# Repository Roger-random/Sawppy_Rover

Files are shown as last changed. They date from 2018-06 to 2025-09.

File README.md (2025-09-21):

# Sawppy the Rover

Sawppy is a motorized model of Mars rovers Curiosity and Perseverance. It faithfully reproduces
the [Rocker-Bogie suspension kinematics](https://en.wikipedia.org/wiki/Rocker-bogie) of real
rovers and is intended to be a hardware platform for future software projects in autonomous
operation. Go forth and boldly explore the back yard, Sawppy!

All information for building Sawppy is free and public open source for anyone to build their
own. Build instructions can be found
[under the docs subdirectory](docs/).

Sawppy the Rover was inspired by [JPL's Open Source Rover project](https://github.com/nasa-jpl/open-source-rover).
Most of the differences between Sawppy and its JPL inspiration were motivated by a desire to reduce cost
and complexity. JPL's rover is designed for education, to be assembled by a school team and give a robust
foundation for structured curriculum. Sawppy is more suited for individual hobbyists like myself who are
happy to tinker and willing to make some trade-offs to lower cost.

The budget was __$500__, see [price breakdown here](docs/Price%20breakdown.md).
Getting to that price point required the following changes:

* Motorization: Instead of using gearmotors with encoders managed by RoboClaw motor controllers,
moving the wheels will be done with serial bus servo motors. For more information on these devices,
please see [this article on Hackaday.com](https://hackaday.com/2018/07/05/wrangling-rc-servos-becoming-a-hassle-try-serial-bus-servos/).
* Construction Method: Instead of using the [Actobotics construction system](https://www.servocity.com/actobotics),
Sawppy will be built from [Misumi HFS3 aluminum extrusions](https://us.misumi-ec.com/vona2/detail/110300465870/)
connected by 3D-printed plastic parts. For more information on this construction technique, please
see [this article on Hackaday.com](https://hackaday.com/2018/05/08/how-to-build-anything-out-of-aluminum-extrusion-and-3d-printed-brackets/).

These two major design goals can be summarized as: **S**ervo **A**ctuated **W**heels,
**P**rinted **I**nterconnect **F**or **E**xtrusion. The acronym SAWPIFE led to the nickedname "Sawppy".

# Development Status

**Status Update, Perseverance Landing Edition**

Generating web traffic was never an objective of my Sawppy project so I hadn't kept an eye on the
statistics, but I looked at it just now and noticed a distinct rise over the past two weeks. I
guess the successful landing of Perseverance rover on Mars motivated a lot of people to think about
3D-printing their own rover here on Earth. Welcome, fellow rover fans!

Here's a quick summary past and future for fans new and old alike:

What you see on this project page is what I now refer to as "Sawppy V1". It was my first project
that I documented with the explicit goal of helping others build their own. In contrast to most
of my other projects which were just to show an example and/or notes to remind myself later. I was
happy to see that many people have accepted my invitation and built their own rovers.
(See "Sawppy Builders" log entries on [Sawppy's Hackaday.io page](https://hackaday.io/project/158208).)
I appreciate constructive feedback submitted by Sawppy rover builders from around the world,
and have been pondering how I can evolve future Sawppy versions to address feedback.

One persistent line of feedback was that Sawppy was still too complex and expensive for some rover
fans, even though Sawppy was designed to be more affordable and simpler than the JPL Open Source
Rover that inspired it. It is true I built Sawppy for myself and others with roughly my level of
skill and budget. This translated to an audience of mostly adult hobbyists and some students of
college and high school age who can drop $500 USD on a project.

To address the audience left out of the fun by Sawppy V1, my current step in Sawppy evolution is
"Micro Sawppy". I am designing and developing a smaller, simpler, and more affordable rover. One
that I want to be accessible to elementary school age students (with adult supervision) with a
target parts cost of $100 USD. I also want to write the instructions to be more exact and prescriptive.
Sawppy V1 instructions had several areas that were left open to builder preference, something I've
learned is confusing to beginners who lacked the experience to have a preference.

Micro Sawppy also serves as my testbed for several ideas for 3D-printed rover construction that,
if successful, I want to adapt and scale up to a "Sawppy V2". This future rover would be roughly
the same size as Sawppy V1. But I want to make it easier to build, more adaptable to variations,
and a lower base cost target of $400 USD.

For latest updates and/or more details, I post my development progress to the
[Sawppy category on my personal blog](https://newscrewdriver.com/category/projects/sawppy-the-rover/).

**Sawppy version 1.0**

This milestone includes a motorized rolling chassis that is mechanically functional.
The remaining areas (electrical, software, etc.) are still very immature, just barely enough
to validate mechanical chassis function. Click this image for a YouTube video illustrating
the chassis in action, climbing a backpack that is almost double the height of wheel diameter.

Sawppy conquers a backpack (https://www.youtube.com/watch?v=SEBBMDWgtC4)

**Sawppy version 1.1**

Sawppy has received only minor mechanical changes for this milestone, including the rocker joint
angle limiter visible in action in the backpack demo video above. Most of the attention has been
on software, with contributions by the Sawppy community.

# Control Software
A Sawppy builder can now choose from many Sawppy software options. Roughly in order of power and complexity, they are:

* **Simplest**: Wired control [running on an Arduino](https://github.com/Roger-random/Sawppy_Rover/tree/master/arduino_sawppy) instead of Raspberry Pi. Created as a [backup control option](https://newscrewdriver.com/2019/05/20/sawppy-roving-with-wired-handheld-controller/) in noisy RF environments where WiFi is unreliable. It also happens to feature the bare-bones version of Sawppy geometry calculations. Wired control meant skipping all the overhead of wireless communication. Cutting out all HTML code also meant this is a good basis for other control mechanisms: send desired speed and direction into Arduino and let it handle Sawppy chassis geometry calculation.
Alternatively, it allows interfacing with anything that can communicate with an Arduino.  Here's a wiring diagram contributed by [Martin](https://hackaday.io/Plaville)
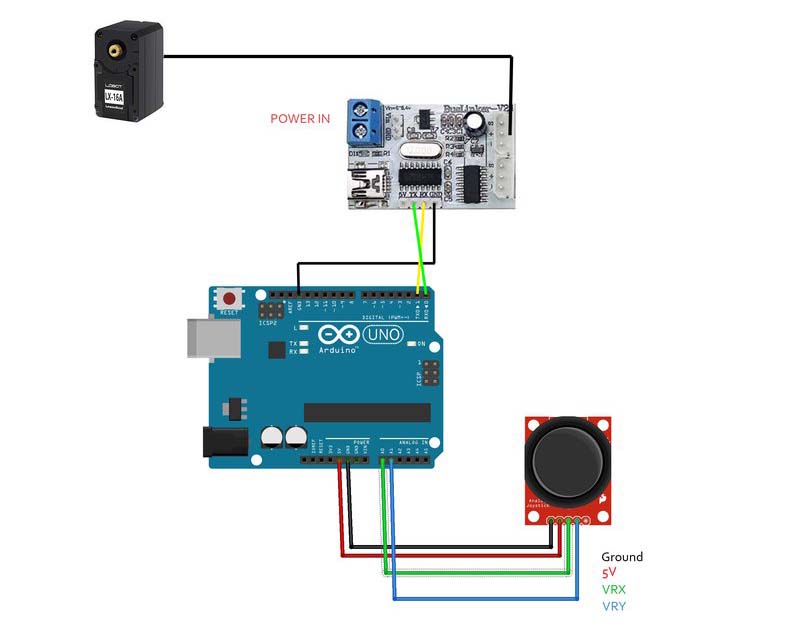
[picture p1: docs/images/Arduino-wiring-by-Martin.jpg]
Arduino wiring diagram by martin


* **Original**: HTML-based wireless teleoperation software stack [modified from SGVHAK rover](/docs/SGVHAK%20Rover%20Software.md). This was written to be easy for others to understand and modify.
* **R/C control**: [lightly modified from my SGVHAK rover software](https://github.com/mw46d/SGVHAK_Rover) by Marco Walther (mw46d) for a Raspberry Pi-based way to interface with traditional remote control receivers.

Plus several options for turning Sawppy into a [ROS](http://ros.org) robotics platform.

* **ROS Kinetic**: [heavily modified from my SGVHAK rover software](https://github.com/mw46d/Sawppy_ROS) by Marco Walther (mw46d) which translates ROS `/cmd_vel` commands into Sawppy movement. This is a good stepping stone beyond original Sawppy software.

* **ROS Melodic**: [a ground-up rewrite of a ROS-centric stack](https://github.com/srmainwaring/curio) by Rhys Mainwaring (srmainwaring) is extensive and powerful, and includes support for RViz visualation and Gazebo simulation. Going beyond responding to `/cmd_vel` commands, it also calculates `/odom` by interpolating LX-16A position encoder ~270 degree feedback into full 360 degrees. Plus visualizing rover state in RViz, and files to put a digital Sawppy in Gazebo robot simulation environment.two

* **ROS2 Humble**: [a version of Swappy the Rover for ROS2](https://github.com/mgonzs13/ros2_rover) by Miguel Ángel González Santamarta
includes a C++ and Python version of the lx16a controller and supports teleoperation with a PS3 joystick controller.  A hukuyo laser rangefinder is also supported.

# Modifications From Rover Builders

Many people who built their own Sawppy rover are also people who love to tinker
and experiment. As a result these rovers reflect the individuality of their
builder. Some of these builders have shared their work with the community,
see the [`modifications` folder](/modifications) for more information.

# Other Project Resources

* [Project page on Hackaday.io](https://hackaday.io/project/158208-sawppy-the-rover)
* [Build blog](https://newscrewdriver.com/category/projects/sawppy-the-rover/)
* [Live Onshape CAD file "Sawppy the Rover"](https://cad.onshape.com/documents/43678ef564a43281c83e1aef/w/392bbf8745395bc24367a35c/e/9bd6bbb7aba50a97523d14f2)

# Financial Support

Sawppy is shared free of charge, but builders in the United States may choose to buy some parts via
[Amazon affiliate links](docs/AmazonAssociate.md)
which will send a small sales commission to Sawppy's creator.

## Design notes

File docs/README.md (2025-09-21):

# Instructions

This directory has information for building your own Sawppy the Rover.
Some of the tools required are listed in the [tools list](Tools.md).

All Sawppy information is shared freely. Those who wish to support this
project may choose to purchase certain parts via
[Amazon affiliate links.](AmazonAssociate.md)
(This does not increase your purchase price.)

## 3D Printed Components
[General overview](Print%20Overview.md) of 3D-printed rover parts.

Details:
* [Servo accessories](Print%20Servo%20Parts.md)
* [Steering knuckle](Print%20Steering%20Knuckle.md)
* [Fixed knuckle](Print%20Fixed%20Knuckle.md)
* [Wheel](Print%20Wheel.md)
* [Wheel hub](Print%20Wheel%20Hub.md)
* [Corner Steering Joints](Print%20Corner%20Steering%20Joints.md)
* [Suspension Bogie Joints](Print%20Suspension%20Bogie%20Joints.md)
* [Suspension Rocker Joints](Print%20Suspension%20Rocker%20Joints.md)
* [Main Body Box Corners](Print%20Body%20Box%20Corners.md)
* [Differential](Print%20Differential.md)
* [M3 Nut Installation Tool](Print%20M3%20Installation%20Tool.md)

## Customized Metal Components
* [15mm square aluminum extrusion beams](Misumi%20HFS%203.md)
* [8mm diameter shafts](Shaft8mm.md)

## Mass-produced Components
* __Turnbuckles__ are used to connect both sides of rocker-bogie suspension together,
see the end of [this document](AssembleRocker.md). The two connection endpoints
need to accomodate M3 fasteners as used in the rover, and the distance between
connection endpoints should be roughly 5cm - 7.5cm. Example:
[Hobbypark 16617](https://www.amazon.com/dp/B01H5PZKMK)
is seen in the assembly pictures.
* __"608" Bearings__ are widespread. It's the type used in products like
rollerblades, skateboards, and scooters. Since Sawppy does not run bearings at
high speeds or put heavy loads on them, expensive
[industrial strength 608 bearings](https://www.mcmaster.com/608-ball-bearings)
are unnecessary. Shop around for
[inexpensive alternatives](https://www.amazon.com/dp/B073ST742Z),
they'll probably suffice for a hobbyist rover.
* __M3 Heat Set Inserts__ give metal threads for 3D-printed parts which are more
durable than threads tapped into printed plastic. Sawppy's default design is sized
for [these inserts](https://www.amazon.com/gp/product/B077CHFGVT) on my printer,
and reportedly works well with [these inserts](https://www.mcmaster.com/94180a333)
as well.
* [Purchased Parts List](Parts%20List.md)

## Mechanical Assembly
For an overview of the construction technique used here, combining aluminum extrusion beams with
3D printed connectors plus using design-specific M3 nut installation tools, please
[see this article on Hackaday.com](https://hackaday.com/2018/05/08/how-to-build-anything-out-of-aluminum-extrusion-and-3d-printed-brackets/).

If any part of the assembly instructions are unclear, consult
[the CAD file](https://cad.onshape.com/documents/43678ef564a43281c83e1aef/w/392bbf8745395bc24367a35c/e/9bd6bbb7aba50a97523d14f2)
to see how parts are supposed to fit together.

* [Servo Actuator Module](AssembleActuatorModule.md)
* [Wheel Drive Modules](AssembleDriveModules.md)
* [Suspension Pivot Joints](AssemblePivotJoints.md)
* [Main Rover Body](AssembleBody.md)
* [Suspension Differential](AssembleDifferential.md)
* [Suspension Bogie](AssembleBogie.md)
* [Suspension Rocker and final assembly](AssembleRocker.md)

Once all the wheels are attached to the suspension via M3x16mm bolts, your Sawppy will be mechanically complete!

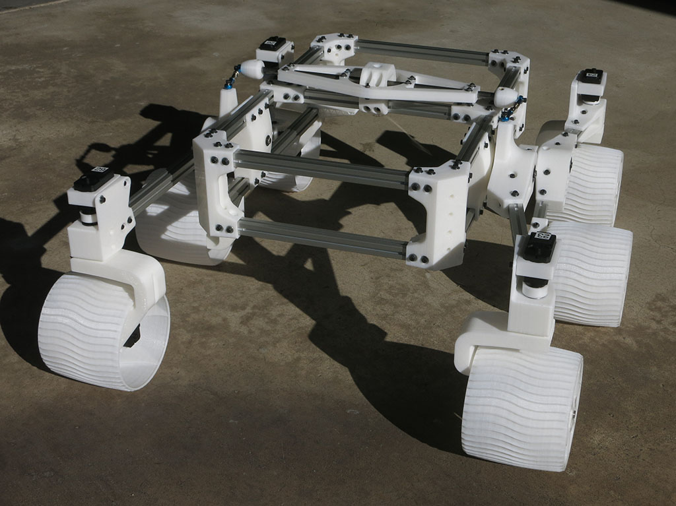
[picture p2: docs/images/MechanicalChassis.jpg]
Mechanical chassis


## Electronic Schematic

A bare-bones Sawppy build will have the following electronic components:
* A 2-cell lithium polymer battery. (Visible in pictures is a 30C 5200mAh RC
monster truck battery)
* A power switch
* Because the battery can deliver up to 150A and nothing on the rover can
tolerate more than a few amps, a [10A fuse to protect against short circuits](https://newscrewdriver.com/2018/06/06/powering-sawppy-the-rover/  ).
* A volt meter to monitor battery voltage.
* A [voltage regulator](https://newscrewdriver.com/2017/07/27/powering-the-raspberry-pi-3-with-mp1584-voltage-step-down-converter/) to convert battery power to 5V.
* A Raspberry Pi 3 powered by 5V regulator output, either via micro USB port or GPIO voltage pins.
* A USB cable connecting Raspberry Pi 3 to serial bus translator board.
* Ten serial bus servos connected in parallel to the translator board. See
[documentation on wiring details](wiring/Wiring.md) contributed by
[knickels](https://github.com/NickelsLab).

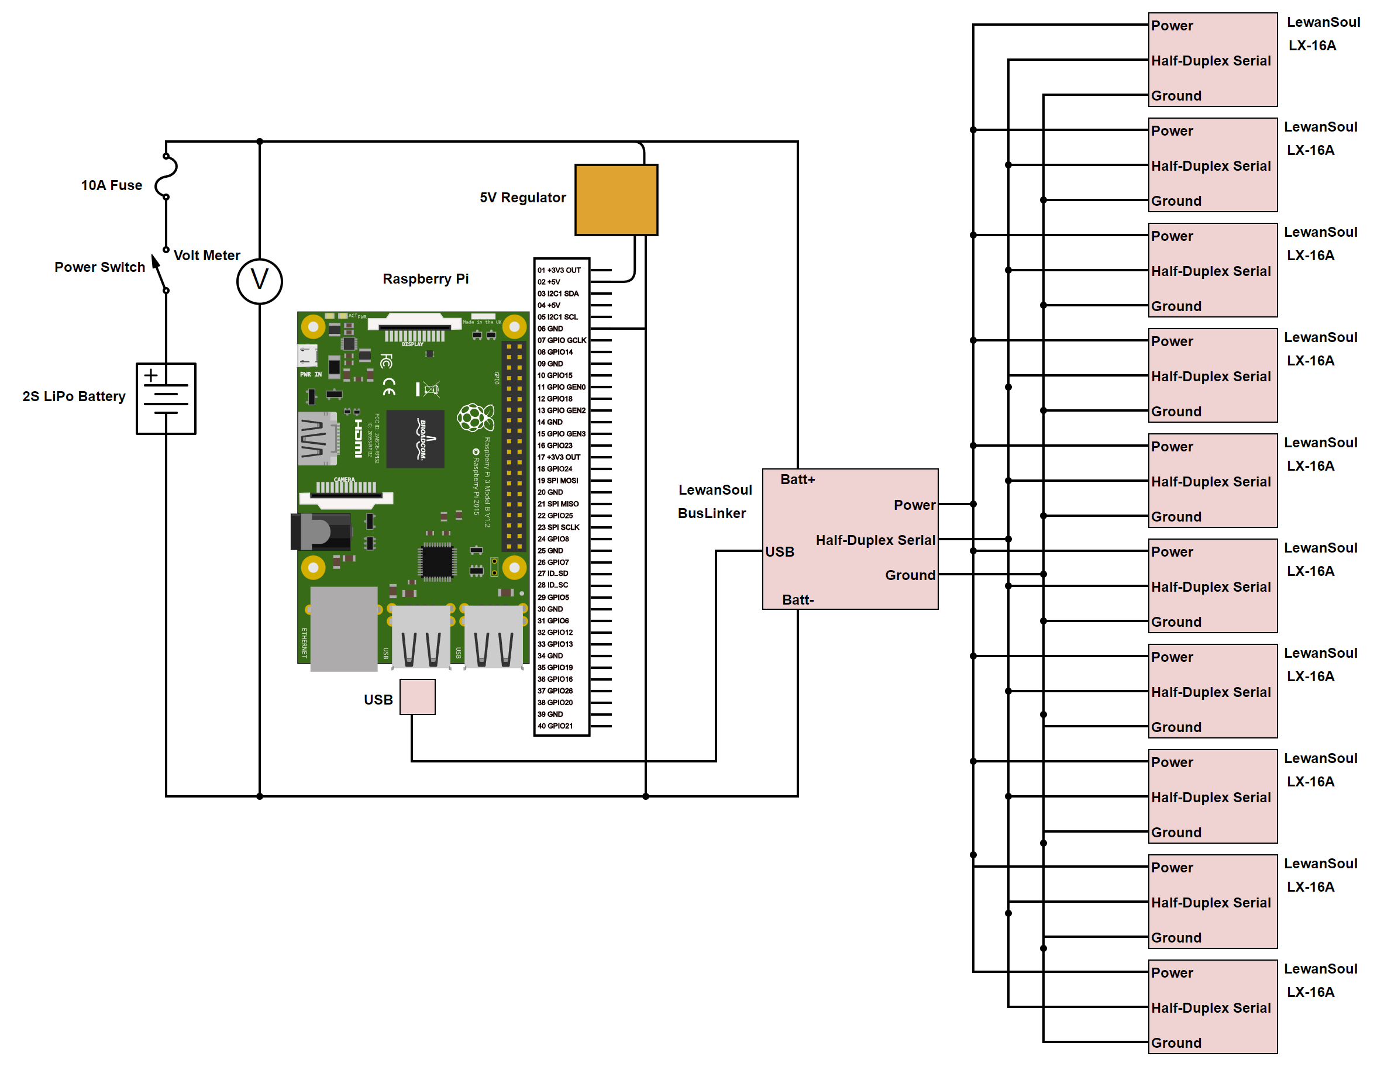
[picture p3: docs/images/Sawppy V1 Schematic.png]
Schematic

[Click here to open schematic in Digi-Key's web-based Scheme-It tool.](https://www.digikey.com/schemeit/project/sawppy-v1-EKLPGFO401M0)

Optional components visible in some Sawppy pictures:
* A [USB webcam](https://newscrewdriver.com/2018/06/19/sawppy-the-backyard-rover/).
* Google [AIY Vision kit](https://newscrewdriver.com/2018/06/18/sawppy-the-rovers-mast-cameras/).
* A dual-band wireless router for [greater range and access to 5GHz band](https://newscrewdriver.com/2018/07/15/sawppy-the-rover-receives-wifi-upgrade-increases-range/).

# Control Software
A Sawppy builder can now choose from many Sawppy software options. They are documented in [README.md#control-software](../README.md#control-software)

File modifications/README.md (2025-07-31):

# Modifications

This directory tracks modifications to Sawppy made by other rover builders.

## Bob Krause, Inventor Studios

A FIRST Robotics team improved Sawppy's design with better configurability.
See more information [here](bob_krause/README.md)

## Quinn Morley

The Qualification Model Rover Demonstrator for Deep Drilling is a scaled-up
version of Sawppy which will serve as a prototype drilling platform testbed.
See more information on [design blog](https://www.quinnmorley.com/2019/02/qmrd3-rover-testbed.html)
and [Github repo](https://github.com/Shootquinn/QMRD3)

## Marco Walther (mw46d)

* Dynamixel AX-12 brackets
* 25D geared motors with encoders

More info [here](Marco_Walther/README.md)

## Kevin Nickels, Trinity University
Trinity Robotics version of Sawppy is named TRIPPY, and has the following revisions:
 * LewanSoul LX-224 brackets
 * LewanSoul LX-224 brackets with captured nuts instead of threads
 * Used M3 Screws as steering axle SetScrews instead of heat-set inserts
 * Modified Arduinio Nano Joystick to use RJ9 connector & phone cord
 * Added holster to hold joystick when not in use

 See more information [here](kevin_nickels/README.md)

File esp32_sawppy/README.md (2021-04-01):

# ESP32 Sawppy Brain
This directory is a PlatformIO project for a Sawppy brain built using an ESP32 development kit.
Using the ESP-IDF framework, individual components are organized into FreeRTOS tasks.

This is written to support Micro Sawppy development, which uses generic RC micro servos and
DRV8833 DC motor driver ICs. It is not yet able to support LX-16A serial bus servos used in
Sawppy V1.

For more details please see project build log: https://newscrewdriver.com/tag/micro-sawppy/

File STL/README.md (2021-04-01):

# Sawppy Rover STL
This directory contains a snapshot of Sawppy rover STL files.
These files will be some distance behind the state of the art, but guaranteed to have been tested.
Onshape CAD file that generated these STL files is available publicly. See documentation directory
for details.

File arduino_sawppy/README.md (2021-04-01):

# Arduino Sawppy Controller
This directory is an Arduino sketch, intending to give Sawppy rover a wired joystick controller
alternative to default WiFi wireless control. Target platform is ATmega328-based Arduino Nano.

Target rover platform is Sawppy V1, based around the LewanSoul/HiWonder LX-16A serial bus servo.
It has not (yet?) been adapted to rovers built on different hardware.

More details on Sawppy build blog, start here and look at adjacent blog entries.
https://newscrewdriver.com/2019/05/20/sawppy-roving-with-wired-handheld-controller/

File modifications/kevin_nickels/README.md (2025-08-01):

# Modifications made by Kevin Nickels, Trinity University

Dr. Nickels has made a TRIPPY - a variant of the Sawppy rover at Trinity University in San Antonio, TX.  He has made several minor modifications to the design during the build.   The name TRIPPY evolved from Trinity-SAWPPY, but could stand for "Trinity Robotics Instructional Planetary Platform".  It's purpose is to give Engineering students at Trinity University in San Antonio a robust platform to develop on top of, and to learn about the world of open-source hardware.

## Table of Contents
 * [LewanSoul LX-224 brackets](#lx-224-servos)
 * [Used M3 Screws as steering axle SetScrews instead of heat-set inserts](#m3-setscrews)
 * [Modified Arduinio Nano Joystick to use RJ9 connector & phone cord](#joystick-controller-modifications)
 * [Added holster to hold joystick when not in use](#joystick-holster)

## Overview

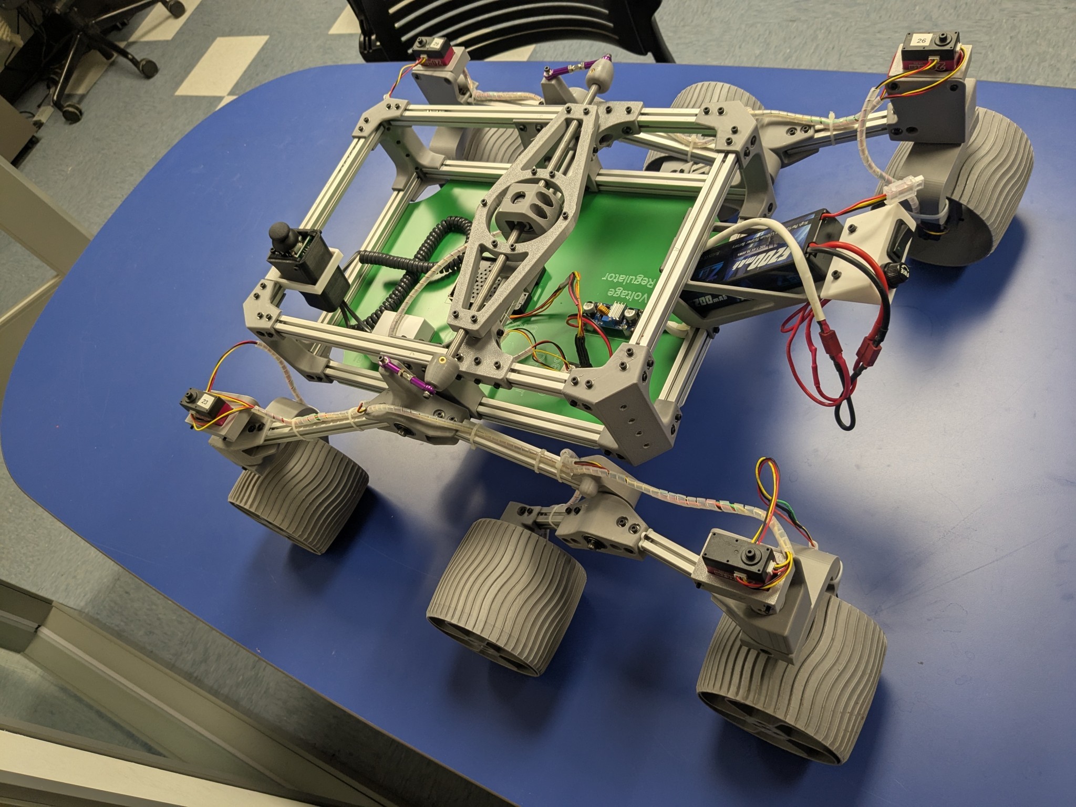
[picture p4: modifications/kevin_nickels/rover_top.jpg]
rover_top

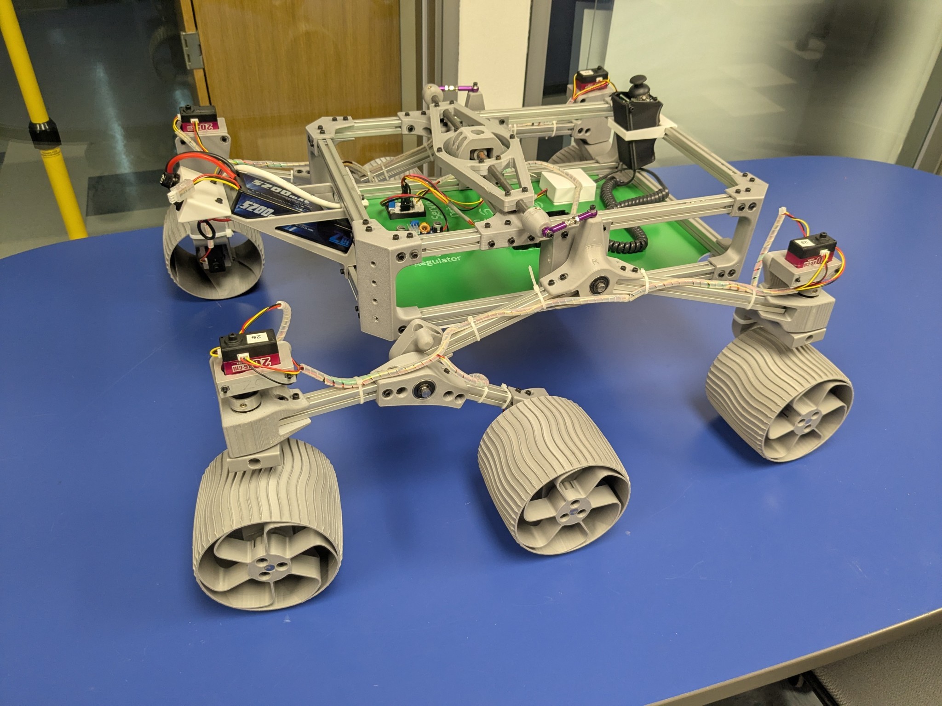
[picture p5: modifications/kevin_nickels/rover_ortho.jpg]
rover_ortho


## LX-224 Servos

The [LX-16A](https://www.amazon.com/Hiwonder-LX-16A-Robotic-Controller-Control/dp/B073XY5NT1) was out of stock when I went to acquire my parts, so I ordered the very similar [LX-224](https://www.amazon.com/LX-224-Serial-Controller-Connectors-Bearing/dp/B0817YWHNL).  I created a LX-224 bracket per the original design, see [my OnShape Sawppy Copy](https://cad.onshape.com/documents/7f40e51e085505c60163b9a8/w/9308f0417bc9c0c20e3ccf9f/e/5f2c482cad123d78f392508a), LX-224 branch, LX-224 Part Studio.
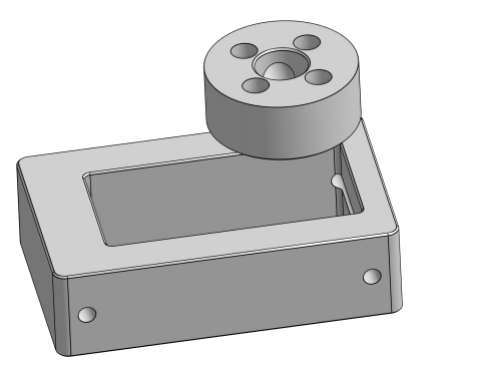
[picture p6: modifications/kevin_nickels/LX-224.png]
LewanSoul LX-224 bracket
 

Since I've had problems with threads, and even threaded inserts, pulling out of plastic before, I also generated an alternative bracket in [the same OnShape CAD, branch LX-224 Bracket w Captured Nuts](https://cad.onshape.com/documents/7f40e51e085505c60163b9a8/w/f72775573146bf34f38f572e/e/5f2c482cad123d78f392508a).  This is designed to be used with [M3x40mm screws](https://www.amazon.com/BNUOK-120pcs-Socket-Threads-Spanner/dp/B0DJQFXKHG/).

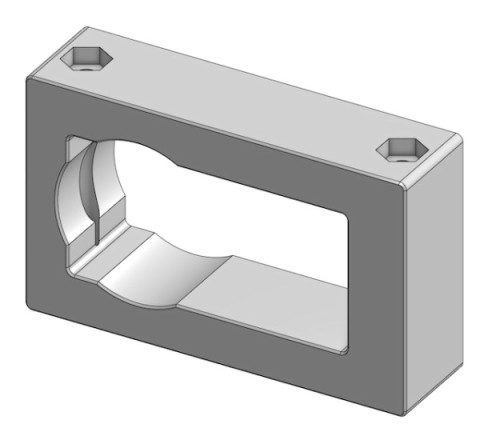
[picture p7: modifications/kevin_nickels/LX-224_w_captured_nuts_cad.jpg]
CAD rendering of LX-224 servo bracket featuring captured nuts for enhanced strength, showing the bracket attached to a steering knuckle within a mechanical assembly.


## M3 SetScrews
As was mentioned in the Discussion section of [CJ - a sawppy variant](https://hackaday.io/project/165094-cj-a-sawppy-variant) on Hackaday, some of us have had issues with heat-set inserts pulling out.  As shown in this CAD and the pictures below, I ended up printing a Nut Carriage to get good strength and print resolution in the XY direction, then printing the knuckle in the standard orientation, so that the M3 nut won't spin when tightened against the flat in the 8mm shaft.  Then, I used an M3x16 screw as a setscrew instead of the tiny ones called out in the original.  We'll see how this holds up over time!

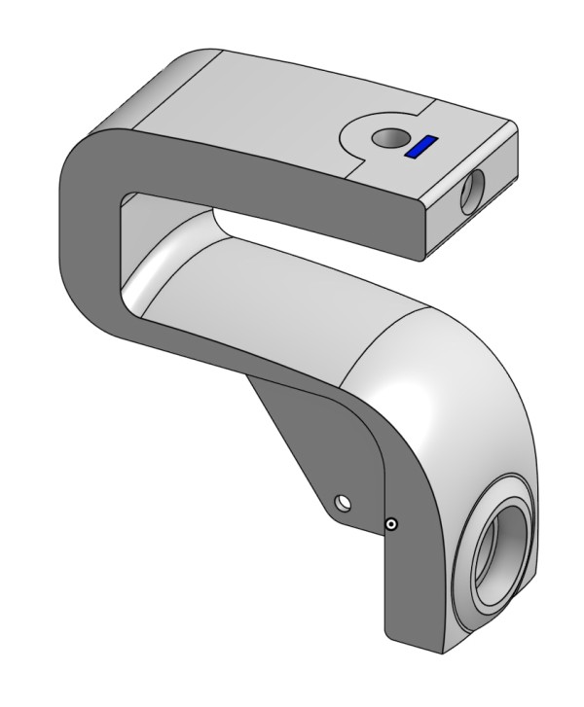
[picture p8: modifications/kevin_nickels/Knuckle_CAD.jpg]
CAD of steering knuckle with nut insert

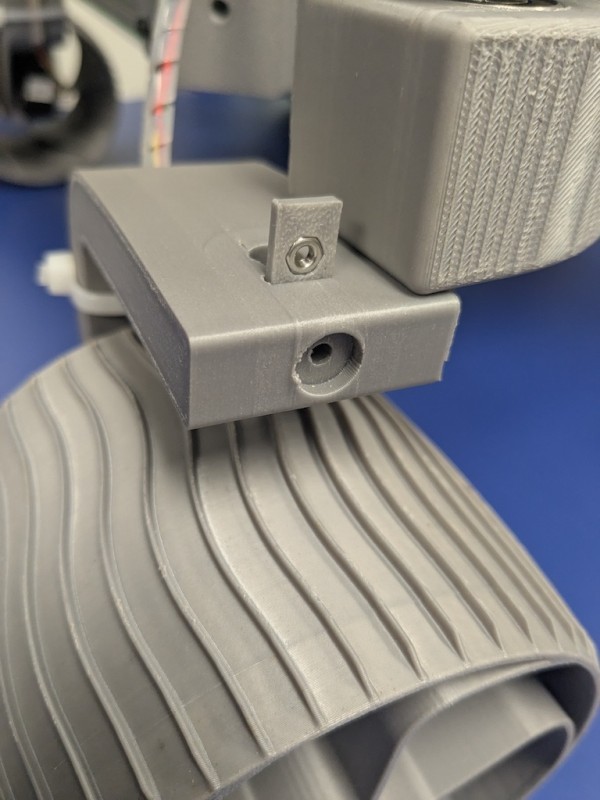
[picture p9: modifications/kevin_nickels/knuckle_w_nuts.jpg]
image of steering knuckle with nut insert

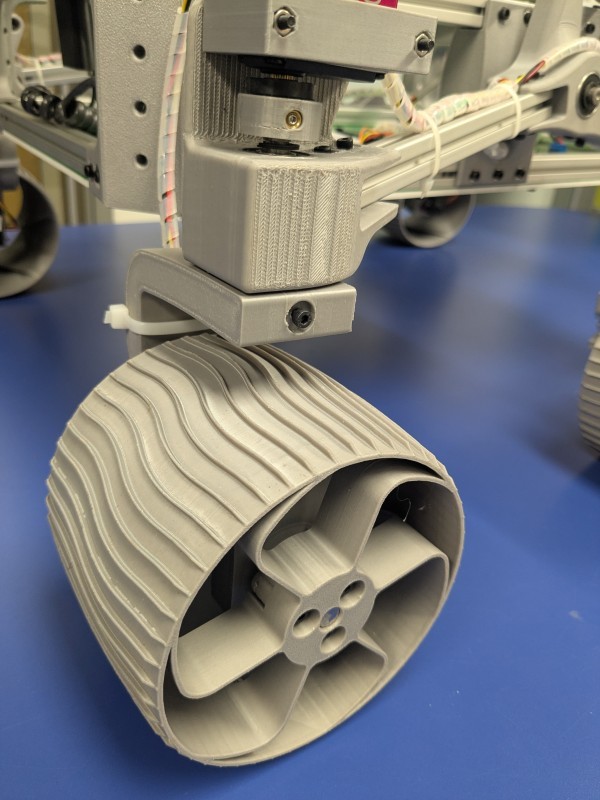
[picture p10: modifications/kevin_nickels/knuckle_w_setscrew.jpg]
image of steering knuckle with nut insert installed


## Joystick Controller Modifications
I also modified the [Handheld Arduino Joystick controller](https://cad.onshape.com/documents/47ee84411a76e86eae57ea0f/w/f70ae835a2d548c4b95fa46e/e/c8538a52492e953cdcdd3db5) to accept an [RJ9](https://www.ebay.com/itm/317094616170) so that I can connect my controller to my rover with a standard coiled phone cord.

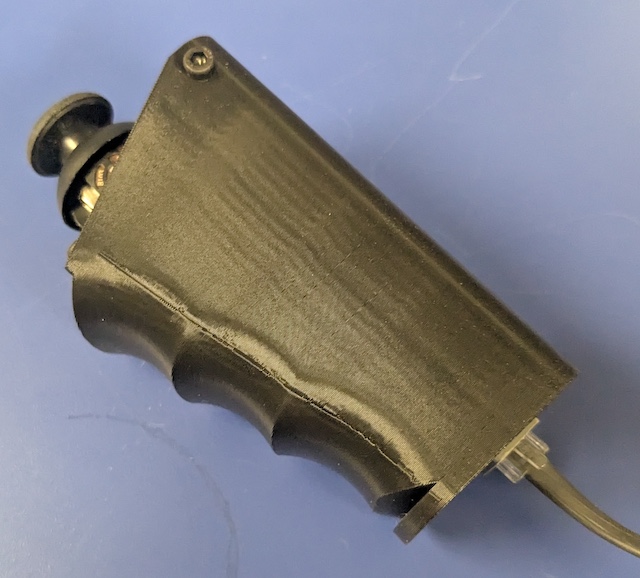
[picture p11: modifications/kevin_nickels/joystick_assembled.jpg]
Picture of assmbled joystick

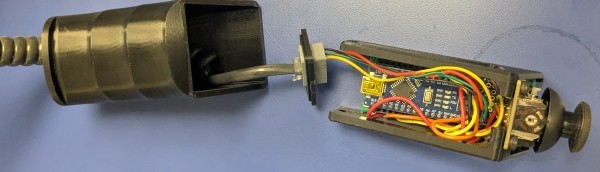
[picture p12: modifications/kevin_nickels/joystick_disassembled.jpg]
Picture of disassembled joystick

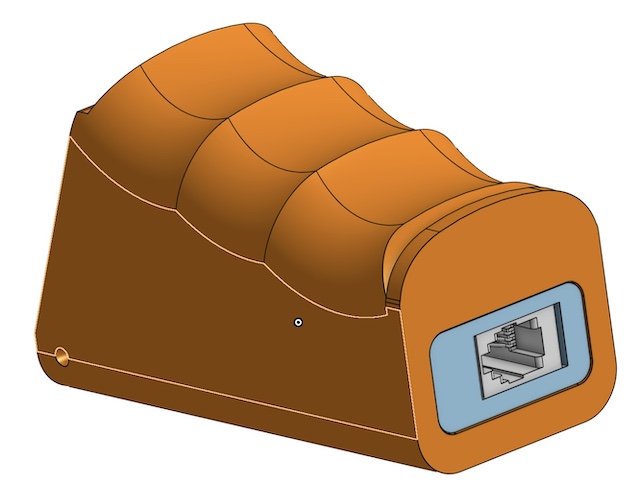
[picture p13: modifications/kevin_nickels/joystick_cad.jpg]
CAD of joystick with RJ9


## Joystick Holster
Finally, I added a holster to the [Handheld Arduino Joystick controller](https://cad.onshape.com/documents/47ee84411a76e86eae57ea0f/w/f70ae835a2d548c4b95fa46e/e/d239459ff7d458760645b579) to accept an [RJ9](https://www.ebay.com/itm/317094616170) so that I can connect my controller to my rover with a standard coiled phone cord.

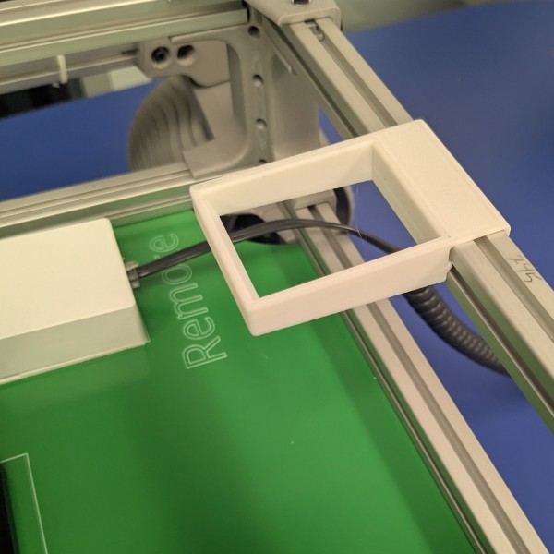
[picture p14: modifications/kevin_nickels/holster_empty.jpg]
Image of holster without joystick

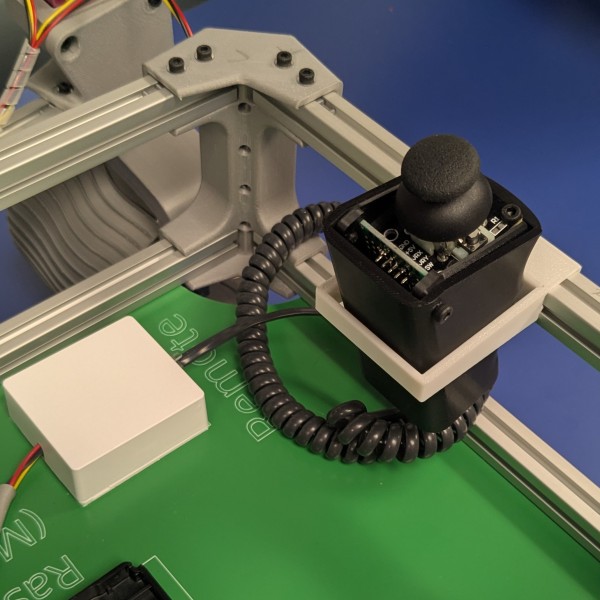
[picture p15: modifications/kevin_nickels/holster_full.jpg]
Image of holster with joystick


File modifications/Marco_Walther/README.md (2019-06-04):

# mw46d Additions

* I created some extra parts to interface the Dynamixel AX-12's with the original parts. But my LX-17 servos arrived in time, so I did not really try the AX-12s.
* I created motified knuckles to use 25D geared motors with shaft-encoders.
(https://www.aliexpress.com/item/6V-100-210-300RPM-Encoder-Motor-DC-Gear-Motor-with-Worm-Gear-Torque-Locking/32914332902.html) I'm using the 100rpm versions of the motor
and they work very well and allow me to get the encoder readings and use those for speed/distance calculations. The only downside is, that I have to deal with many more
cables:-( Originally, each side had just three, now I have 3 (for the steering servos) + 3 * 6 (for the drive motors).
* A nice little Display just for fun;-) Found it on the original NASA JPL rover model and liked it;-)

A little night excursion: https://youtu.be/rvCmtjlanaQ

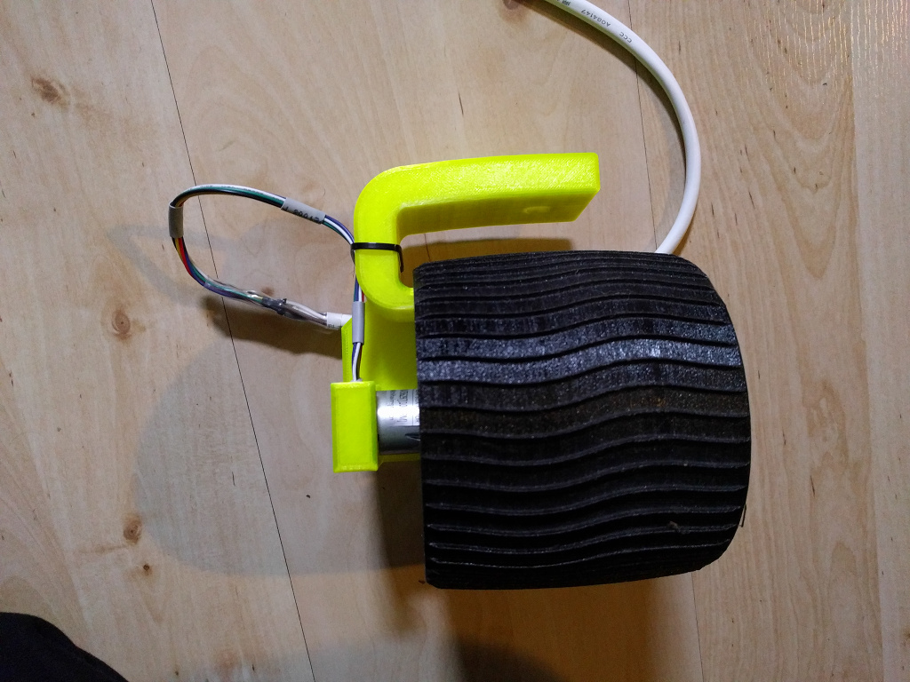
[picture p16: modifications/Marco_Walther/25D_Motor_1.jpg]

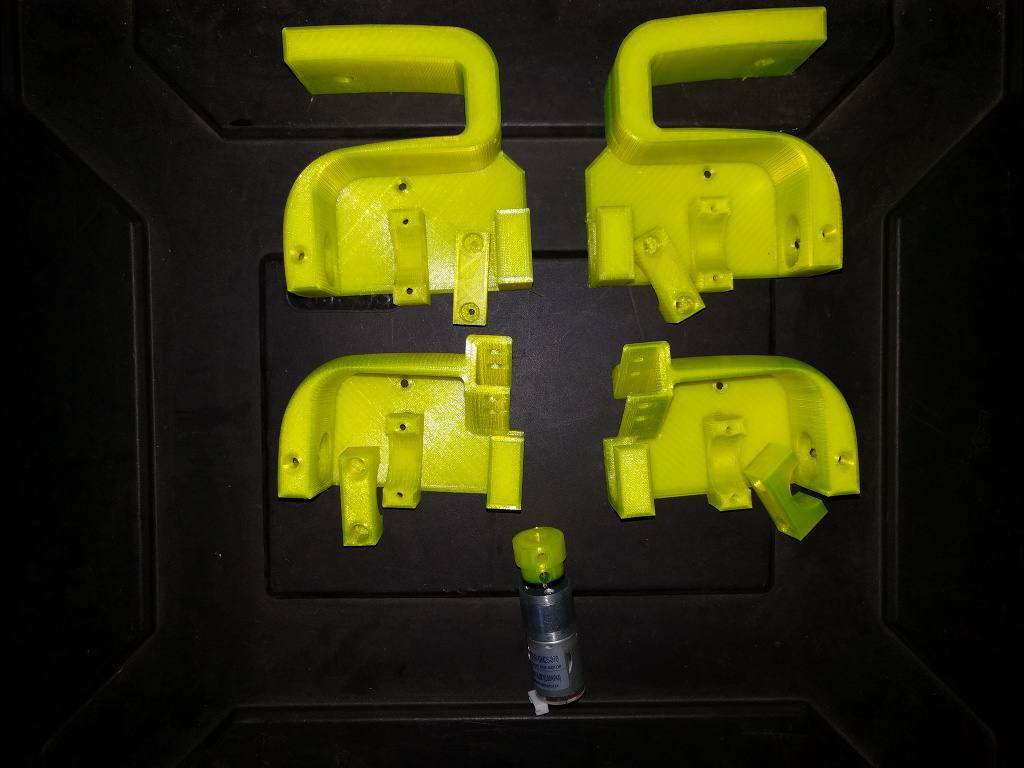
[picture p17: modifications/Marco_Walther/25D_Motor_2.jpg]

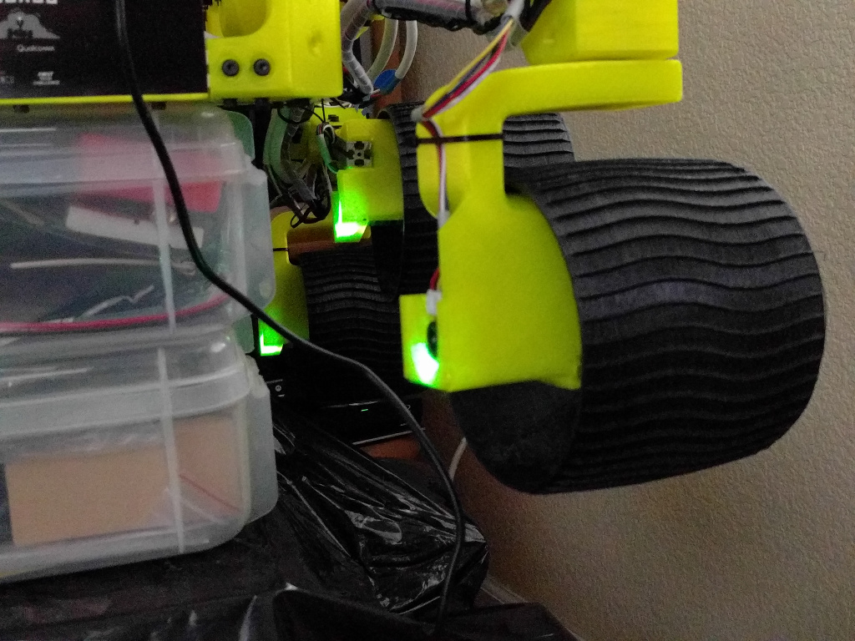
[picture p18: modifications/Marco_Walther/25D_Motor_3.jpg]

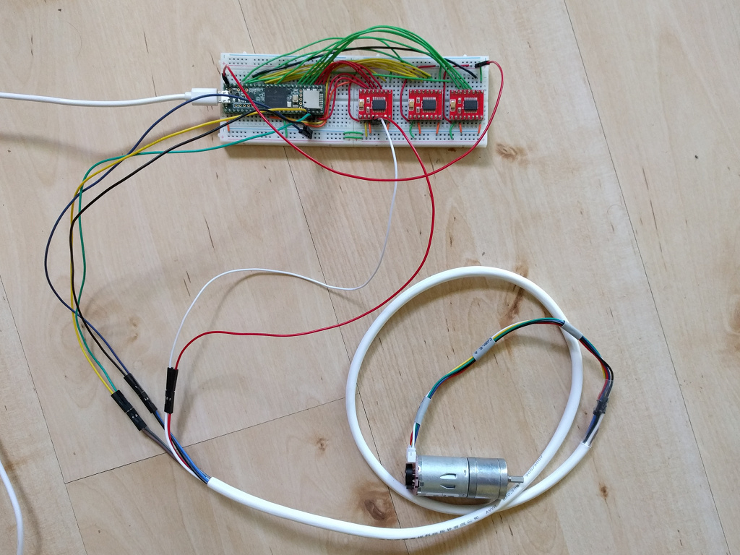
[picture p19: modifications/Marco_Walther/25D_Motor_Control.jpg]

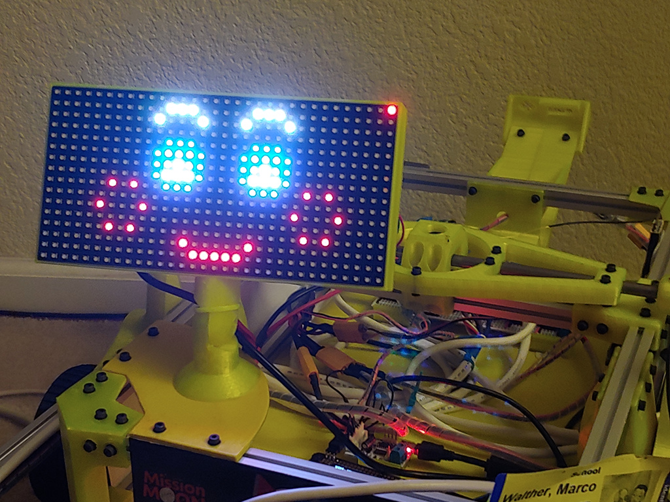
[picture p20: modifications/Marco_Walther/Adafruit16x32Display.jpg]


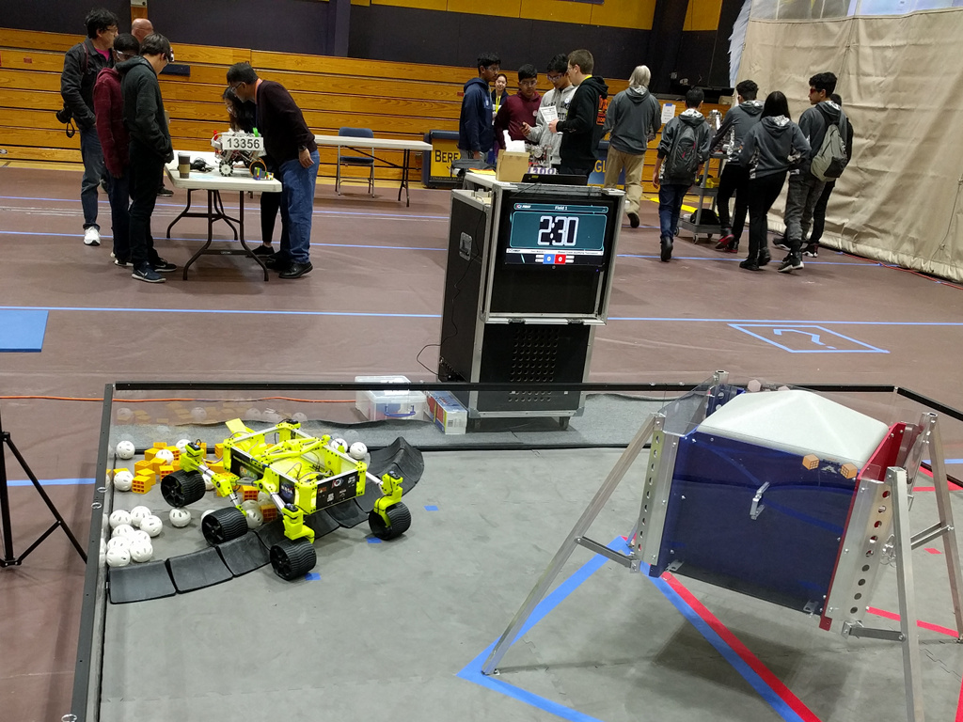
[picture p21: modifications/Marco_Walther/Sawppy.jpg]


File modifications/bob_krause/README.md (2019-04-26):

# Bob Krause, Inventor Studios

(The following information was first posted on Sawppy's Hackaday.io project
discussions section [here](https://hackaday.io/project/158208-sawppy-the-rover/discussion-116870))

_____

Our focus at this point is to increase the configurability of the design, as
you can see in the list of changes we’ve made so far that’s included below. 

* Wheel width can be changed
  * Wheel width changeable
  * Steerable knuckle width varies with wheel width
  * Fixed knuckle width varies with wheel width
* Wheel rim and tire can be printed as separate parts of a dual-extrusion
printer job
* Beam width & height can be changed
  * All 3D printed components that accept beams varies based on beam dimensions
* LX-16A brackets now accept heat-sets so that servos are held more tightly

* The geometry of the LX-16A bracket changed. 
  * The orientation of the servo is rotated 180 degrees to fit narrow knuckles
  and narrow tires.

The area we’re focusing on next is support for drive-train and control systems
that will move the bot much (much) faster than the LX-16A servos currently
allow. The first step in that direction is to design in FTC-compatible (First
Technical Challenge) components, which we have an almost endless supply of
parts laying around the lab. Driving a bogie suspended robot around on rough
terrian at high speeds will likely require adding shock dampeners to the
suspension.

Our longer-term aspiration is to create a more flexible robot design tool
that allows designers to create robots with different dimensions,
drive-trains, suspensions, control systems, and accessories.

We’ve made our copy of the OnShape document public. It’s named
SawppyRover.neobobkrause. You can link to it here
https://cad.onshape.com/documents/aaa3eec885d174f48744d770/w/a9ccb2ae8a9fa3bfab65a3f5/e/02e39956ce53a7a4a720a4aa

Here are some shots of some wheels and knuckles we've printed that are
narrower (65mm). One wheel has a TPU tire on a PLA rim. The other rim was
printed using transparent PETG. The third photo shows the narrow fixed knuckle
from the inside. Also note that the orientation of the servo has been rotated
180 degrees.

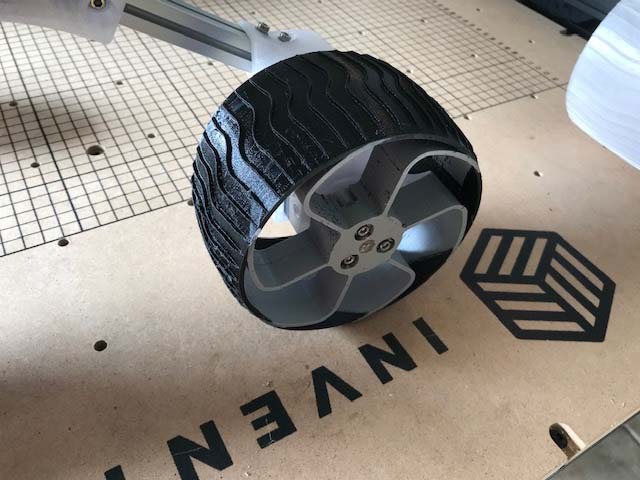
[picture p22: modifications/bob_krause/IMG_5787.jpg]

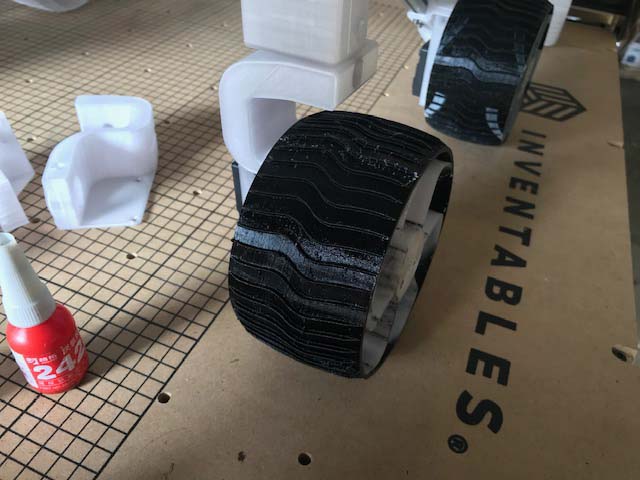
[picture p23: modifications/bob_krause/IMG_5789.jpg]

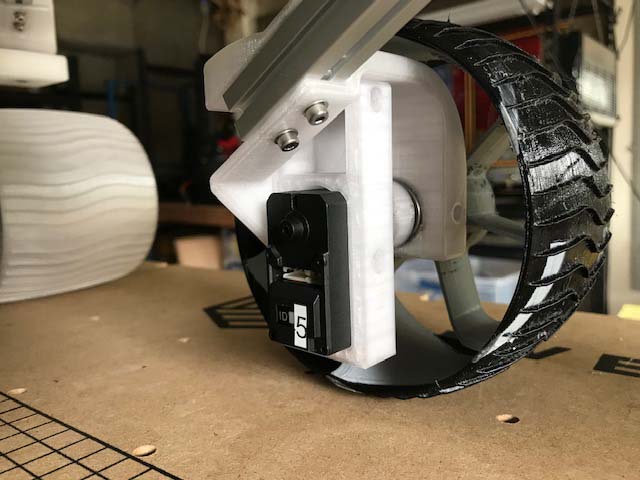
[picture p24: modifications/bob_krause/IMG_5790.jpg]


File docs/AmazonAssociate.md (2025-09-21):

# Support Sawppy via Amazon Associates Program
Sawppy the Rover is a project done out of love of our interplanetary robotic
explorers Curiosity and Perseverance. Sawppy's design and instructions for
construction are shared with other rover lovers free of charge under the
permissive MIT license.

Some very generous people have offered to donate to
help the project. I have declined offers of direct donation, but I have
set up an Amazon Affiliates account based on suggestion. If an aspiring
rover builder buys components from Amazon (USA) using the links
below, they will pay the same price but Amazon will send a (very small)
percentage of the sale to me as sales commission.
Here is the boilerplate disclosure:
_As an Amazon Associate I earn from qualifying purchases._

I have other links to Amazon products scattered throughout Sawppy
documentation, but they are generic links that do not earn commission.
This is the only page with affiliate links.

__Name__ | __Specific__ | __Generic__ | __Comments__
--- | --- | --- | ---
_**Mechanical**_ |
LX-16A Bundle | [Hiwonder](https://amzn.to/2WAm4Wl) | | Each bundle includes 5 servos and 1 BusLinker. A rover needs 10 servos and 1 BusLinker.
LX-16A | [Hiwonder](https://amzn.to/2z0VVqV) | | Individual replacements, or if bundle is not available.
BusLinker | [TTL Board](https://amzn.to/2T4V8vZ) | | Only one needed per rover. Do not need to buy separately if buying LX-16A bundle.
Turnbuckle | [Hobbypark](https://amzn.to/3cCZ5Qg) | | Eyes at end should fit M3 fasteners
Bearings | [SACKORANGE](https://amzn.to/3fMBiiG) | [608](https://amzn.to/2WyPHHO) | Inexpensive generics are fine
M3 Heat Set Inserts | [Initeq](https://amzn.to/2WWCF5Q) | | 3D printed parts are sized to this outer diameter
Cable sleeve | [Techflex](https://amzn.to/366gdLy) | | Wire management
_**Electronics and Communication**_ |
Servo Cable Connectors (LX-224) | | [JST2.0 P3 Connectors](https://www.amazon.com/80Pcs-JST-2-0-Connector-Plug/dp/B0DMW522GM) | To connect LX-224 servos to BusLinker
Servo Cable Connectors (LX-16A) | | [Mini-SPOX Pins](https://www.newark.com/molex/08-70-1040/contact-socket-22awg-crimp/dp/54H5573) [Mini-SPOX  Housing](https://www.newark.com/molex/50-37-5033/connector-rcpt-3pos-1row-2-5mm/dp/57H1785)| To connect LX-16A servos to BusLinker
Crimper for Mini-SPOX | | [iCrimp XH2.54mm](https://www.amazon.com/dp/B00YGLKBSK?th=1) | To crimp Mini-SPOX pins
Raspberry Pi | [Pi 3 Model B](https://amzn.to/3cArxSI) | [Raspberry Pi](https://amzn.to/2AythOm) | 3B+ now available, Pi 4 should also work
microSD Card | [Sandisk Extreme 32GB](https://amzn.to/3bET8AS) | | For Raspberry Pi
Wireless Router | [Asus RT-AC1200](https://amzn.to/2TcYBst) | | (Optional) Easier to find a channel on 5GHz WiFi in crowded places.
Arduino Nano | [ELEGOO](https://amzn.to/3bvAFXy) | [Other Clones](https://amzn.to/2LzvqLK) | (Optional) backup [wired control](https://github.com/Roger-random/Sawppy_Rover/tree/master/docs#wired-arduino)
Joystick module | | [WMYCONGCONG](https://amzn.to/3fNR0KB) | (Optional) backup [wired control](https://github.com/Roger-random/Sawppy_Rover/tree/master/docs#wired-arduino)
_**Power System**_ |
Battery | [Floureon](https://amzn.to/3dQJ21r) | [2S LiPo](https://amzn.to/2WWz2ge) | Typically sold for remote control cars/boats/aircraft.
Battery Connector | [Adoreco](https://amzn.to/2WZhikp) | [Deans T Plug](https://amzn.to/3dPsbfh) | Commodity plug
Inline Fuse Holder | [Nilight](https://amzn.to/3cCqfXf) | | Holds automotive style blade fuses
Fuse Assortment | [BESTTOYHOME](https://amzn.to/2WY3zKA) | | 5A fuse allows normal operations while protecting against abuse
5V Regulator | [Qunqi](https://amzn.to/2AyxH7T) | [MP1584EN](https://amzn.to/361HHlK) | Converts raw battery power to 5V for Raspberry Pi
Battery Charger | [Tenergy TB6-B](https://amzn.to/3dNjMZV) | [LiPo Charger](https://amzn.to/2TcliwL) | Cell balancing capability preferred
Power Switch | [Conwork SPST](https://amzn.to/2ApRB4L) | | (Optional) This one fits in my power panel
Voltage LED | [Baite](https://amzn.to/364aeqD) | | (Optional) This one fits in my power panel
Low Battery Alarm | [Woafly](https://amzn.to/3fVtOdt) | | (Optional) Connected to battery's balancing plug

### Legend:
* __Name__ used in Sawppy documentation.
* __Specific__ This is the specific item for my own Sawppy and I am happy with my first hand experience.
* __Generic__ This is the general category of items. Not specifically on board my rover but they should all work just fine. (If it's a link to a specific item: I was not happy with my experience, but it was nominally usable.)
* __Comments__ Addendum

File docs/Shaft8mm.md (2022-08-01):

# 8mm metal shafts

Sawppy the Rover uses 8mm shafts anywhere there is a rotary motion that whose load is borne by 608 type bearings.
* Wheel axle drive shaft for all 6 wheels.
* Steering shaft for 4 corner motors.
* 2 Suspension bogie pivot point, one on each side.
* 2 Suspension rocker pivot point, one on each side.

Below are instructions on how to build your own shafts.

---

Sawppy also uses an 8mm shaft as main backbone for the differential that spans width of the rover. This shaft is
300mm long and hosts no retaining clips, so there are no grooves to cut. It host set screws at either end,
but they do not convey torque and detents are not required to be cut.

## Shaft stock selection

Any metal shaft should work, as long as it has the appropriate 8mm diameter to fit snugly within 608 type bearings used.
As these shafts are not spun to high speeds, carry high torque, or mesh with other machinery, Sawppy does not require
high precision industrial machinery shafts. (Example: unnecessarily expensive high precision shafts from
[Misumi](https://us.misumi-ec.com/vona2/detail/110300086920/?ProductCode=SFMR8-300)
and [McMaster-Carr](https://www.mcmaster.com/1265k64)) Low precision round bar stock are a fraction of the cost and will
suffice. The worst that would happen with low precision shafts is that wheels may be a little wobblier.

Aluminum shafts (example: McMaster-Carr [catalog #4634t34](https://www.mcmaster.com/4634t34)) are inexpensive and strong
enough for normal rover operation. If the rover will be carrying additional equipment, or taken to public events with
exposure to young children, consider upgrading to steel shafts for extra strength. (Example: McMaster-Carr
[catalog #8920k26](https://www.mcmaster.com/8920k26) is used in the rover seen in assembly pictures.)

## Retaining clips

The shafts are kept in place by small retaining clips. (Sometimes called e-clips.) The precise size of these clips
are not critical for rover function, they just need to be small enough to grip on a groove in a 8mm diameter shaft
and large enough to hold against a 608 bearing. The clips used in the assembly pictures are McMaster-Carr
[catalog #97431a310](https://www.mcmaster.com/#97431a310) designed for 5/16-inch shafts.
As we will be cutting our own grooves for these retaining clips (see next item)
we can adjust groove dimension to suit physical attributes like clip thickness.

## Grooves for retaining clips

The retaining clips will need grooves cut into the shafts. Ideally this can be done on a metalworking lathe, but
it can be done with a drill and a high speed motor ("Dremel") tool in a [poor-man's lathe](https://newscrewdriver.com/2018/05/18/poor-mans-lathe-cutting-a-steering-shaft-with-drill-and-dremel/).
And there are many options in between, limited only by your resourcesfulness and creativity.

## Detents for set screws

The driving and steering shafts will need a flat detent cut into them for set screws. If precise metalworking
tools are not available, they can be cut by [clamping the shaft in a vise and use a metal file](https://newscrewdriver.com/2018/06/20/improve-motor-shafts-with-larger-flatter-detents-and-apply-loctite-to-set-screws/).

The detent for the wheel hubs needs to be cut at least 1mm into the shaft, so that the 8mm set screw doesn't stick out from the hub. This can be measured with callipers - the shaft should be no more than 7mm when measured inside the detent. The rest of the detents don't need to be any specific depth, as long as they are flat enough for the set screw to grab the shaft.

## Dimensions

These drawing dimensions are in millimeters, and they are incomplete because the precise width of retaining grooves
will depend on the retaining clip used and also on what tools are available to cut those grooves. For the rocker and bogie
shafts, their end pieces can be as narrow as fabrication technique (and skill) permit, but 1-2mm is a good target range.

#### Wheel axle drive shaft

Make 6 copies, one for each wheel. The 9mm segment is for servo coupler and needs detent. The 22mm segment is
for a wheel, and the inside edge will be for the wheel hub and needs a detent.

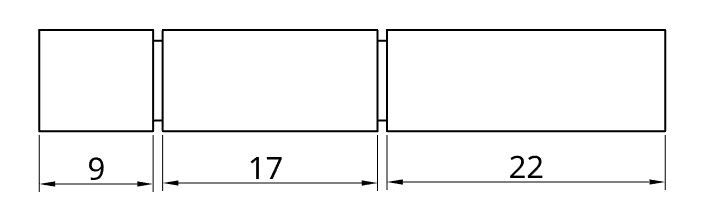
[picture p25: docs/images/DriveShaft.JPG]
Drive shaft dimensions


#### Steering shaft

Make 4 copies, one for each corner. The 9mm segment is for servo coupler and needs detent. The 15mm segment is
for a steering knuckle and needs a detent at its center.

Steer shaft dimensions

#### Bogie pivot shaft

Make 2 copies, one for each side. No detents necessary.

Bogie shaft dimensions

#### Rocker pivot shaft

Make 2 copies, one for each side. No detents necessary.

Rocker shaft dimensions

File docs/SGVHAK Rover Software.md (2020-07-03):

# SGVHAK Rover Software

While the long-term vision for Sawppy is an autonomous vehicle running on [ROS](http://www.ros.org/)
we have an interim software solution adapted from [SGVHAK Rover](http://bit.ly/sgvhak_rover).
Sawppy running SGVHAK rover software will present a web-based user interface
turning a touchscreen into a joystick to drive a rover as a remote-control
car. (Mouse click and drag can also be used on non-touchscreen devices.) This
is also called a 'teleoperation' mode.

Clone the [SGVHAK Rover software repository](https://github.com/Roger-random/SGVHAK_Rover) 
and follow instructions to install dependencies. (Optional installation of ```virtualenv```
and required installation of Python libraries ```pip install -e .```)
Before proceeding to step "Start Flask", make the modifications below.

The information below are specific to the LewanSoul serial bus servos used
on first Sawppy implementation, but the general concept are applicable to
alternative serial bus servos with modification.

# Before Rover Wiring: Assign Unique ID To Each Servo

Sawppy has ten LewanSoul serial bus servos wired in parallel. In order to tell
them apart, each servo must have an unique identifier different from any other
servo on board the rover. By default, every servo is assigned id #1 at the
factory and must be renamed one at a time. This procedure is also an
opportunity to verify the BusLinker a.k.a. Debug Board is working.

For this step, connect a single servo to BusLinker. Connect a two-cell LiPo
battery to BusLinker power inputs Vin and GND to power the servo. Connect USB
cable to computer.

Single serial servo wired for rename Serial Servo Rename

For Linux (such as Raspberry Pi's Debian or Ubuntu Linux on laptop visible in
picture) run the ```dmesg``` command immediately after plugging in the USB cable
to see which port it has been assigned. The final few lines of output from
running ```dmesg``` should look similar to the following:

```
[ 2980.395126] usb 2-3: new full-speed USB device number 15 using xhci_hcd
[ 2980.568517] usb 2-3: New USB device found, idVendor=1a86, idProduct=7523
[ 2980.568524] usb 2-3: New USB device strings: Mfr=0, Product=2, SerialNumber=0
[ 2980.568528] usb 2-3: Product: USB2.0-Serial
[ 2980.571592] ch341 2-3:1.0: ch341-uart converter detected
[ 2980.582703] usb 2-3: ch341-uart converter now attached to ttyUSB0
```

Write down the final piece of information (in this example ```ttyUSB0```) and
edit the file [```config_lewansoul.json```](https://github.com/Roger-random/SGVHAK_Rover/blob/master/config_lewansoul.json). 
Edit line 4 value for ```port``` accordingly. Once configured, we can run the
LewanSoul support code in [```lewansoul_wrapper.py```](https://github.com/Roger-random/SGVHAK_Rover/blob/master/SGVHAK_Rover/lewansoul_wrapper.py)
as a standalone command line utility. Run it with the command line
```python SGVHAK_Rover/lewansoul_wrapper.py``` and the following help screen
should be displayed.

```
~/SGVHAK_Rover$ python SGVHAK_Rover/lewansoul_wrapper.py
usage: lewansoul_wrapper.py [-h] [-id ID] [-t TIME]
                            [-m MOVE | -q | -r RENAME | -s SPIN | -u | -v]

LewanSoul Serial Servo Command Line Utility

optional arguments:
  -h, --help            show this help message and exit
  -id ID, --id ID       Servo identifier integer 0-253. 254 is broadcast ID.
  -t TIME, --time TIME  Time duration for action
  -m MOVE, --move MOVE  Move servo to specified position 0-1000
  -q, --queryid         Query for servo ID
  -r RENAME, --rename RENAME
                        Rename servo identifier
  -s SPIN, --spin SPIN  Spin the motor at a specified speed from -1000 to 1000
  -u, --unload          Power down servo motor
  -v, --voltage         Read current input voltage
```

With a single LewanSoul serial bus servo connected, send an ID broadcast
query to determine its current ID. If it is new from factory, it is likely
to have ID of 1.

```
~/SGVHAK_Rover$ python SGVHAK_Rover/lewansoul_wrapper.py -q
Broadcasting servo ID query
Servo ID 1 responded to query
```

Change this servo's ID. This example shows changing ID from 1 to 30.

```
~/SGVHAK_Rover$ python SGVHAK_Rover/lewansoul_wrapper.py --id 1 --rename 30
Checking the specified servo ID 1 is on the serial network.
Checking the specified destination servo ID 30 is not already taken.
Renaming servo ID 1 to 30
Verifying the servo now answers to new ID
Servo successfully renamed to ID 30
```

Give each of our ten servo their own individual ID. The exact values are not
important but they must be ten different IDs. If desired to copy reference
Sawppy implementation, give them ID #20 through #29. Mark each servo with 
their new ID for reference. Sawppy visible in pictures used a label maker
to record each servo ID.

# Servo Placement During Construction

Take note of servo ID in each location. If desired to copy reference Sawppy
implementation, here is a table of servo position along with their ID. This
information is duplicated in [```config_roverchassis.json.sawppy```](https://github.com/Roger-random/SGVHAK_Rover/blob/master/config_roverchassis.json.sawppy)
in JSON format.

|Left |Rolling|Steering| |Steering|Rolling|Right|
|-----|-------|--------|-|--------|-------|-----|
|Front|     25|      23| |      29|     27|Front|
|Mid  |     21|        | |        |     22|Mid  |
|Rear |     20|      24| |      26|     28|Rear |

# Rover Suspension Geometry

If a rover has been modified in a way that changes its suspension geometry
such that wheel positions have shifted, their position needs to be updated
in [```config_roverchassis.json.sawppy```](https://github.com/Roger-random/SGVHAK_Rover/blob/master/config_roverchassis.json.sawppy)
for proper calculation of [Ackermann steering](https://en.wikipedia.org/wiki/Ackermann_steering_geometry)
angles on each of four corner wheels. See section "Physical Geometry" under
"Configurations and Modifications" of [SGVHAK Rover instructions](https://github.com/Roger-random/SGVHAK_Rover).

# Rover Steering Servo Trim

Once rover is standing on its own wheels, use the command line utility again
this time to find center positions for all four steering servos. In a perfect
world a servo's center position 500 will be where a wheel points straight ahead,
but realities of construction mean each rover will have slightly different values.

This example shows starting with 500 then trying position on either side of
center: 510 and 490.

```
:~/SGVHAK_Rover$ python SGVHAK_Rover/lewansoul_wrapper.py --id 30 --move 500
Moving servo 30 to position 500
:~/SGVHAK_Rover$ python SGVHAK_Rover/lewansoul_wrapper.py --id 30 --move 510
Moving servo 30 to position 510
:~/SGVHAK_Rover$ python SGVHAK_Rover/lewansoul_wrapper.py --id 30 --move 490
Moving servo 30 to position 490
```

Update [```config_roverchassis.json.sawppy```](https://github.com/Roger-random/SGVHAK_Rover/blob/master/config_roverchassis.json.sawppy)
with correct center position for each of four steering servos.

NOTE: SGVHAK rover software menu has a "Steering Trim" menu item, but that is
specific to RoboClaw controller used by SGVHAK rover and does not apply to
Sawppy rover.

# Overwrite Rover Chassis Configuration File

Once our ```config_sawppy.json``` has been properly updated, copy
it over ```config_roverchassis.json``` to overwrite SGVHAK rover 
configuration with Sawppy configuration.

# Start Flask

Now our clone of SGVHAK rover software has been reconfigured for our Sawppy
rover build, and we can resume [SGVHAK Rover instructions](https://github.com/Roger-random/SGVHAK_Rover)
from step 'Start Flask' onwards.

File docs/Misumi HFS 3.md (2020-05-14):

# Structural Beams

Sawppy the Rover's aluminum beam structures are from [Misumi's HFS 3-series.](https://us.misumi-ec.com/vona2/detail/110300465870/)
They are 15mm by 15mm square in profile and there are different options for purchase, more details below for aspiring
rover builders in the USA.

Unfortunately, Misumi subsidiaries outside United States (such as Misumi Europe) are not as hobbyist-friendly
selling only to businesses and not individuals. Fortunately, Sawppy design is not picky about the exact extrusion 
profile and any beams 15mm by 15mm square should work with little to no modifications. One such alternative is
[MakerBeamXL](https://www.makerbeam.com/makerbeamxl/) which has been successfully used to build Sawppy rovers by 
[Rhys in Wales](https://hackaday.io/rhys.mainwaring) and [HolgerDK in Denmark](https://hackaday.io/HolgerDK).
Another option is AliExpress, source of
[beams used to build Aussie Sawppy](https://hackaday.io/project/166017-aussie-sawppy/log/164843-aussie-sawppy-parts-procurement).

I've also heard from a rover builder using 15mm wooden beams, which gives the rover a smooth external profile.
There is also an Argentinian contingent investigating 15mm square profile metal tubes. I expect additional modifications
will be necessary for these efforts, but we won't know until these intrepid explorers report their results.

## Aluminum Extrusions Beams for Rover Chassis

The following quantities and lengths are required to build Sawppy:

Quantity | Length (mm) | Purpose
--- | ---: | ---
4 | 385 | Main body box, lengthwise
4 | 245 | Main body box, widthwise
1 | 238 | Main body differential fixed beam
2 | 182 | Suspension member connecting rocker joint to front wheel
2 | 161 | Suspension member connecting rocker joint to bogie joint
2 | 122 | Suspension member connecting bogie joint to mid wheel
2 | 117 | Suspension member connecting bogie joint to rear wheel

## Cost estimate

__Option 1: Cut the beams yourself__

Purchase standard 2-meter lengths of HFS3 from Misumi and cut to length yourself. This is the most economical option if you have
a saw that can cut aluminum. Or if you have more time than money and willing to hacksaw all the pieces by hand.
This is also the best option if you want to experiment with modifying the rover design.

Fortunately Sawppy is designed so precise length is not necessary, and the cut ends don't have to be perfectly square.
An extrusion can be up to 5mm shorter than specified, or have sloped cut ends, and the rover will still work. Such
imperfections can be compensated for with few extra millimeters of space when bolting plastic pieces onto beams.

The above lengths add up to 3922mm. If you are really good with planning and have a very thin saw blade, it is possible to
cut all rover parts out of two 2-meter pieces of extrusion. This has been confirmed by several other rover builders.

2 * $7.40 = $14.80

__Option 2: Order beams from Misumi cut to length__

Misumi offers a configurable length service where they will cut the beams to your specified lengths. This will result
in perfectly square cut ends and the lengths will be very accurate. Misumi guarantees +/- 0.5mm but internet forum
posts indicate in practice it's far more precise than that.

The convenience and precision will cost $42.32.

Misumi precut shopping cart

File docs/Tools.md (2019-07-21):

# Tool List
Access to some tools will be required to build Sawppy the Rover:

| TOOL | NOTES |
|:----:|:-----|
| Drill | |
| 8mm Reamer | Preparing holes in plastic prints for 8mm rods |
| M3 Metric Tap | Threading holes in plastic prints to accept M3 screws |
| Soldering Iron | Used to set threaded inserts into plastic prints |
| 2.5mm Hex (Allen) Wrench | Used for tightening M3 screws |
| 1.5mm Hex (Allen) Wrench | Used for tightening M3 set screws |

## Tools for 8mm Shaft Preparation
The [8mm shafts](Shaft8mm.md) can be prepared to the necessary length with the required detents and retaining clip grooves using various processes. The tools required for their preparation will depend on which tools the builder has access to and feels most comfortable using. Alternatives include:

* Metalworking lathe
* Using a drill and Dremel to cut retaining clip grooves as [documented here](https://newscrewdriver.com/2018/05/18/poor-mans-lathe-cutting-a-steering-shaft-with-drill-and-dremel/) and using a vice and file to cut set screw detents as [documented here](https://newscrewdriver.com/2018/06/20/improve-motor-shafts-with-larger-flatter-detents-and-apply-loctite-to-set-screws/).

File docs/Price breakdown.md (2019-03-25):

# Sawppy the Rover
## $500 Budget breakdown

Sawppy the Rover was designed with the price target of a basic rolling chassis for
under $500 in parts. This chart breaks down general areas of spending.
Prices in this chart are in United States dollars and reflect rough
price range available within the USA. Bargain hunters may be able to
get these parts for closer to $400. On the flip side, I've been told
some of these parts cost significantly more outside of US. This is
only a rough guideline.

| Component | Price | Notes |
|:---:|:-----:|:-----:|
| Raspberry Pi 3 | $50 | Including microSD card, case, and [5V regulator](https://newscrewdriver.com/2017/07/27/powering-the-raspberry-pi-3-with-mp1584-voltage-step-down-converter/) |
| LewanSoul LX-16A servos | $150 | 10 x $15 each |
| LewanSoul USB interface board | $10 | Sometimes called "BusLinker" or "Debug Board" |
| Misc. electronics | $20 | Power switch, volt meter, fuse with holder, wires and connectors |
| Battery pack | $25 | A 5200mAh 2S LiPo battery pack will allow several hours of operation |
| 3D printing filament | $75 | 3 x 1kg spools @ $25 each |
| Aluminum extrusions | $45 | Price for Misumi cutting service. Cut yourself for less, [more details here](Misumi%20HFS%203.md). |
| 8mm shafts | $10 | Price for 8mm steel rod stock, [more details here](Shaft8mm.md). |
| 608 bearings | $20 | |
| Turnbuckles | $10 | |
| Misc. hardware | $75 | Screws, bolts, washers, nuts, heat set inserts. |
| Laser cut acrylic for equipment bay | $10 | |
| Total | $500 | |

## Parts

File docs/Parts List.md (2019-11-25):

# Parts List

## Printed Parts
To Build Sawppy the Rover, you will need to print the following parts. Quantities and notes are listed.

You will need about 3kg of filament to print all the parts.

| QTY | PART | NOTES |
|:---:|:----:|:-----:|
| 88 | Clip2n125 | Print a few extra for spares |
| 12 | Clip3n20 | Print a few extra for spares |
| 6 | Wheel Hub | Print a few extra for spares |
| 10 | LX-16A - Coupler | Print a few extra for spares |
| 10 | LX-16A - Bracket | |
| 6 | Wheel | |
| 4 | Steering Knuckle | |
| 4 | Body Corner | |
| 2 | DiffBrace | |
| 2 | DiffLink | |
| 1 | DiffLower | |
| 1 | DiffUpper | |
| 2 | Rod Support | |
| 1 | Power Panel | |
| 2 | Fixed Knuckle | Mirrored |
| 2 | Front Corner | Mirrored |
| 2 | Rear Corner | Mirrored |
| 2 | Bogie Wheels | Mirrored |
| 2 | Bogie Body | Mirrored |
| 2 | Rocker | Mirrored |
| 2 | Rocker Body Mount | Mirrored |
| 2 | DiffEnd | Mirrored |
| 2 | Battery Tray | Mirrored |

## Shafts
The following are lengths and quantites for the shafts. You should make the differential axle from steel, and the others can be made from aluminum or steel.

If you're careful and/or lucky, you can get all the shaft you need from a pair of 500mm shafts, not counting the 300mm shaft you need for the differential shaft.

Please see [Shaft dimensions](Shaft8mm.md) for more details.

The lengths below are approximate, depending on groove size. The important dimensions are the distances between the grooves.

| QTY | LENGTH | PART |
|:---:|:----:|:-----:|
| 1 | 300 | Differential Shaft |
| 6 | 50 | Wheel Axle Shaft |
| 4 | 61 | Steering Shaft |
| 2 | 66.5 | Suspension Bogie Pivot Point |
| 2 | 84 | Suspension Rocker Pivot Point |

## Hardware

You will also need the following hardware

| QTY | PART | NOTES |
|:---:|:----:|:-----:|
| 10 | LX-16A Servos | |
| 30 | 608 Bearings | |
| 300 | M3x8mm socket head screws | |
|  28 | M3x16mm socket head screws | |
| 300 | M3 washers | |
| 300 | M3 nuts | |
| 100 | M3 threaded inserts | |
| 100 | 5/16" external retaining clips (E-Clips) | See [Shaft dimensions](Shaft8mm.md) for more details |
| 22 | M3x8 set screws | |
| 2 | Turnbuckles | See [Main README](README.md) for more details |
| 40 | [1/4" long Philips #2 brass screw](https://www.mcmaster.com/#98685a220) | |

## Aluminum Extrusions Beams for Rover Chassis

The following quantities and lengths are required to build Sawppy:

Quantity | Length (mm) | Purpose
--- | ---: | ---
4 | 385 | Main body box, lengthwise
4 | 245 | Main body box, widthwise
1 | 238 | Main body differential fixed beam
2 | 182 | Suspension member connecting rocker joint to front wheel
2 | 161 | Suspension member connecting rocker joint to bogie joint
2 | 122 | Suspension member connecting bogie joint to mid wheel
2 | 117 | Suspension member connecting bogie joint to rear wheel

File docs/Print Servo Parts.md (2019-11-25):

# LewanSoul LX-16A shaft coupler and mounting bracket

Information here builds Sawppy with [LewanSoul LX-16A](http://www.lewansoul.com/product/detail-17.html) servos.

**CAD source** [LX-16A](https://cad.onshape.com/documents/43678ef564a43281c83e1aef/w/392bbf8745395bc24367a35c/e/214191f692ee748deef95a8d)

### To use other serial bus servos.

Sawppy's design can be adapted to other similar serial bus servos, for example the [Dynamixel AX-12A](http://www.robotis.us/ax-12a/)
or the [Herkulex DRS-0101](http://www.dongburobot.com/jsp/cms/view.jsp?code=100788).

The conversion process involves making a shaft coupler and a bracket that fits the specific servo and mounts
to the same places (Two M3 screws + 8mm shaft) as the LewanSoul LX-16A actuator module pictured here.
Mechanically, the remainder of the rover would be the same.

## Coupler

The servo coupler connects the serial bus servo's output to the 8mm steel shaft for both steering a wheel or driving a wheel.

**3D Printing STL File:** [LX-16A - Coupler.stl](../STL/LX-16A%20-%20Coupler.stl)

**3D Printing Notes:**
* This coupler will be held on to the shaft via a set screw that will sit inside a bronze heat-set insert. (Installation instructions below.) The hole that hosts the insert needs to be the right diameter to work - too large, and the set screw will push it out. Too small, and the extra plastic will get in the way of the insert. If you're having trouble printing the holes properly, try stepping down to a finer-pitched print layer height.
* We will need 10 of these. Four for steering servos, six for driving servos. Also, considering making an extra coupler or two to keep on hand for repairs.
* Example print durations:
  * Fast PLA rough draft: 16 minutes each * 10 couplers = 2.6 hours total.
  * Slow PETG final draft: 22 minutes each * 10 couplers = 3.6 hours total.

**Post-Processing**

Estimated time: 5 minutes per coupler * 10 couplers = 50 minutes total.

**Tools:**
* 8mm reamer with drill
* Soldering iron or other hot-tipped tool.
* 10-14mm long M3 bolt with washer and hex wrench.

**Parts:**
* 3D printed servo coupler
* M3 heat-set insert

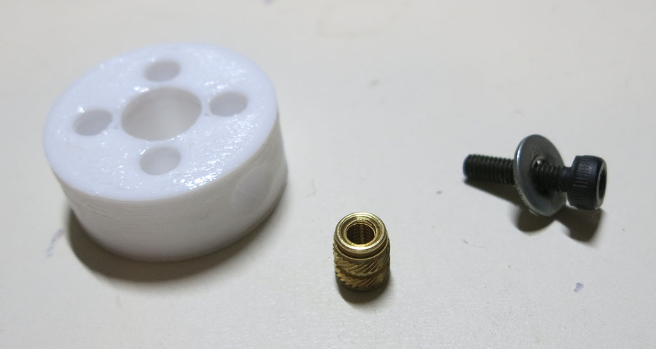
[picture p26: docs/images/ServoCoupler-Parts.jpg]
Servo coupler parts


Just like the wheels, we'll want to clean up the 8mm hole with a reamer so it fits snugly over an 8mm steel shaft.

Then we'll install the heat-set insert. Because the set screw will be pushing against the shaft, installing the
heat-set insert from outside is bad: it'll want to pop back out when we tighten the screw. So for durability we
want to install the heat-set insert from __inside__ the 8mm shaft. To do so we'll need to use a M3 bolt to hold the
insert in place as we get started.

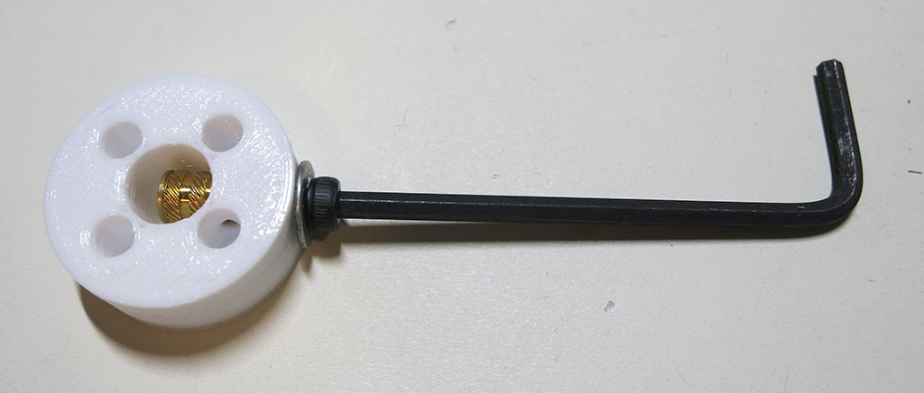
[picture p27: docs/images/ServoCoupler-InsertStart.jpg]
Servo coupler heat set insert held by M3 bolt


Once the M3 bolt is holding the heat-set insert snug against the hole, we can start heating the insert to soften
the surrounding plastic. We can then turn the hex wrench to pull the insert into the softened plastic a bit. Then
we heat a bit more, then we pull a bit more. Don't use a lot of force on the wrench - we're trying to melt into
the plastic, not pull it in with brute force. Using too much force will cause the plastic to move away and bulge
outwards instead of melting into the grooves on the insert.

Servo coupler heating begins

After a few heat-and-turn cycles and the insert is roughly 1/2 to 2/3 of the way installed, we can remove the
bolt because the insert won't fall out anymore. Be careful when removing the M3 bolt as it will be hot.

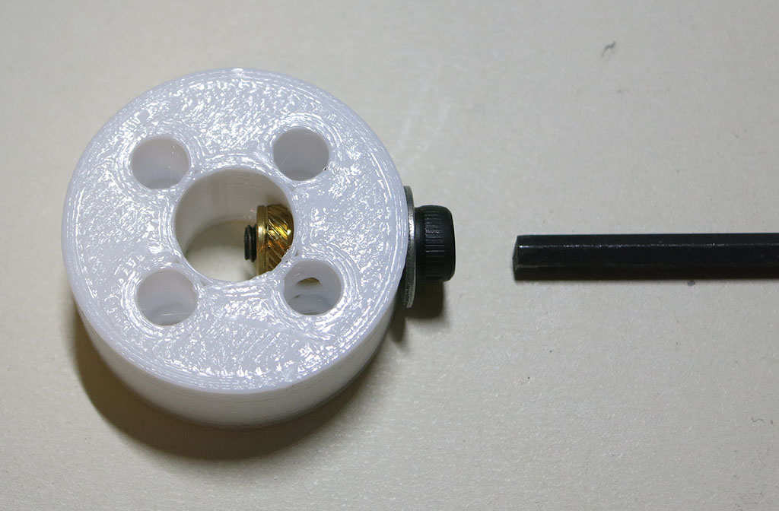
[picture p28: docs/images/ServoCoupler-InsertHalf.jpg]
Servo coupler heat insert halfway


Then we can use the soldering iron to melt the insert the rest of the way.

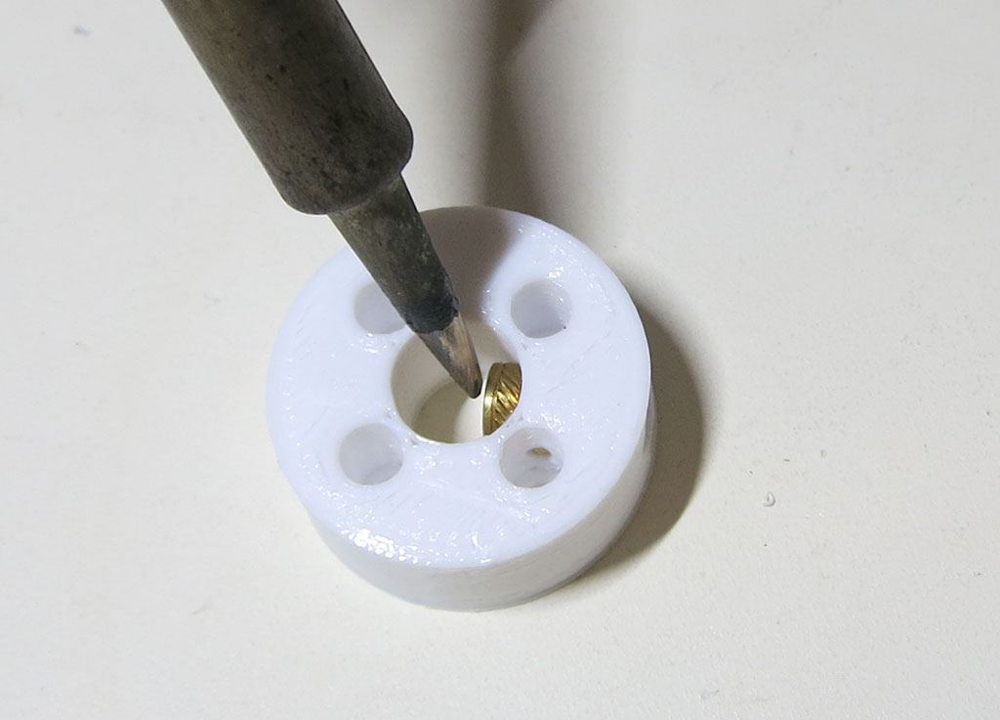
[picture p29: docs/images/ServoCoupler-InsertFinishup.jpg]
Servo coupler heat insert finishing


Installation is complete when the insert is completely in the plastic and no longer sticks out into the center 8mm shaft hole. When looking at the outside hole, we should see a little lip of plastic that the insert has pushed ahead of itself. This lip helps keep the insert in place when the set screw is installed.

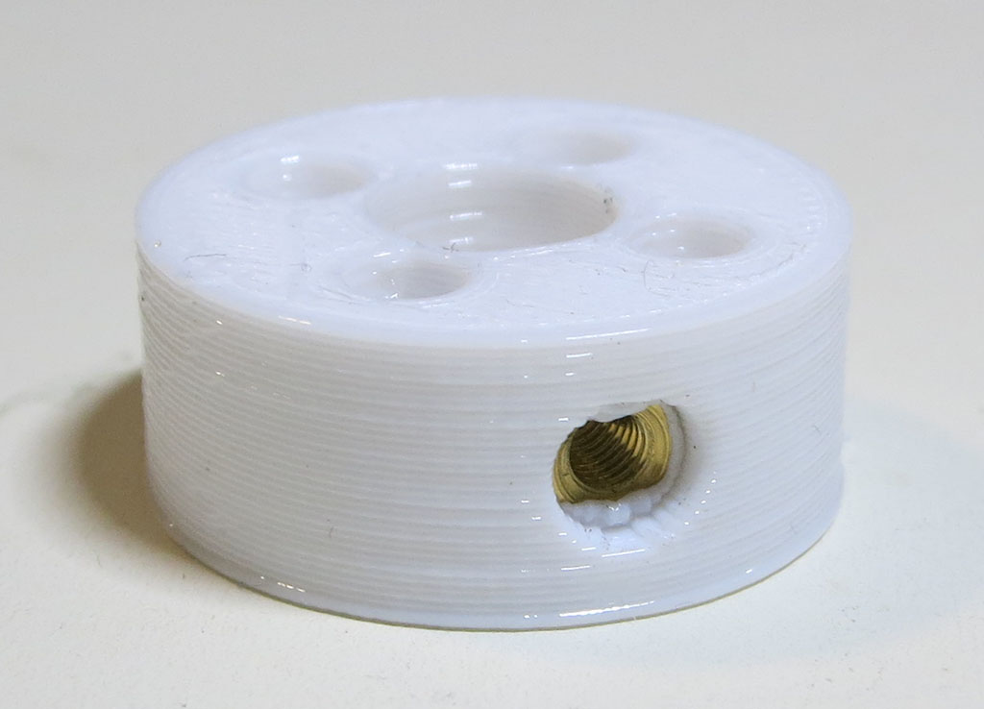
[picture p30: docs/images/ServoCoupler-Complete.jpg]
Servo coupler heat set insert complete


## Bracket

The servo bracket is how each servo is mounted to the rest of Sawppy's chassis, via two M3 threads tapped
in the bracket's plastic. This may be upgraded to M3 threaded heat-set inserts in the future but for now
it seems strong enough for the purpose.

**3D Printing STL File:** [LX-16A - Bracket.stl](../STL/LX-16A%20-%20Bracket.stl)

**3D Printing Notes:**

* Ideally the inner surface of the bracket will conform to the servo exterior snugly, but the preciseness
of fit will depending on individual 3D printers. A perfect fit is when the servo can be inserted with no
effort and it has no room to rattle. If the servo has room to rattle around, or if you need a hammer to
insert the servo, that's not good. Either tune 3D printer settings (possibly [XY compensation](http://manual.slic3r.org/troubleshooting/dimension-errors))
or edit the dimensions in Onshape CAD.
* We will need 10, one for each servo. Also consider making an extra unit or two to keep on hand for repairs.
* Example print durations:
  * Fast PLA rough draft: 38 minutes each * 10 brackets = 6.3 hours total.
  * Slow PETG final draft: 70 minutes each * 10 brackets = 11.6 hours total.

**Post-Processing:**

Estimated time: 1 minutes per bracket * 10 brackets = 10 minutes total.

**Tools:**
* M3 thread tap with handle

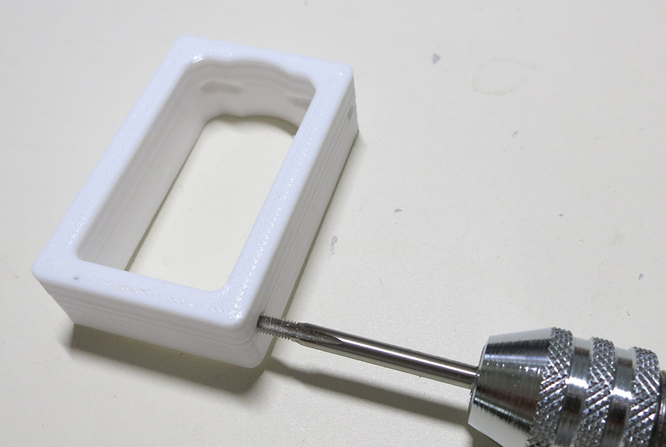
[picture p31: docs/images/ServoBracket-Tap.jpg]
Servo bracket M3 tap


The 3D printer file has four holes, two on each side. You only need to tap two holes on one side,
the other two are spares. The bracket is symmetric so in case of thread damage you can flip the bracket
around to tap the remaining two holes and put the bracket back to work. If they become damaged too, drill
out the damaged thread and make it into a hole large enough for a M3 thread heat-set insert.

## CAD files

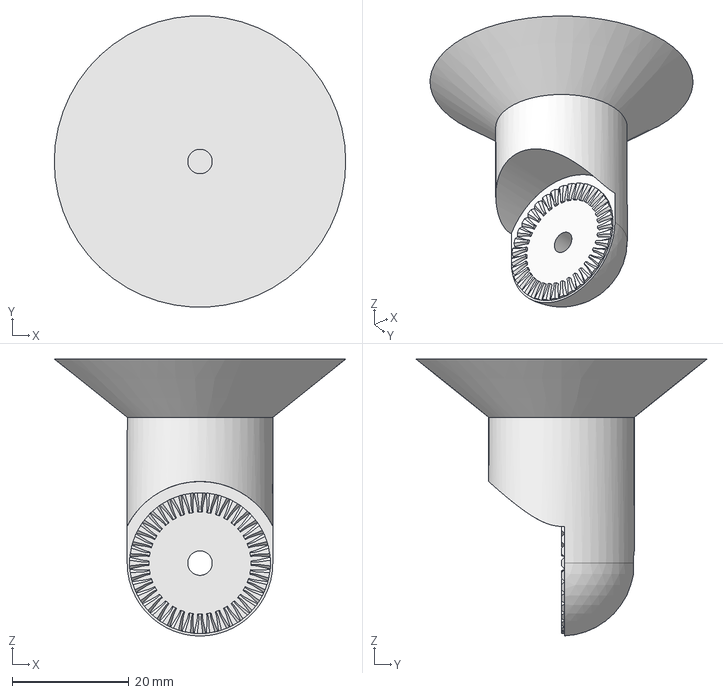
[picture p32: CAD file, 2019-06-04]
modifications/Marco_Walther/DisplayBottom.FCStd
50.0 x 49.9 x 47.5 mm

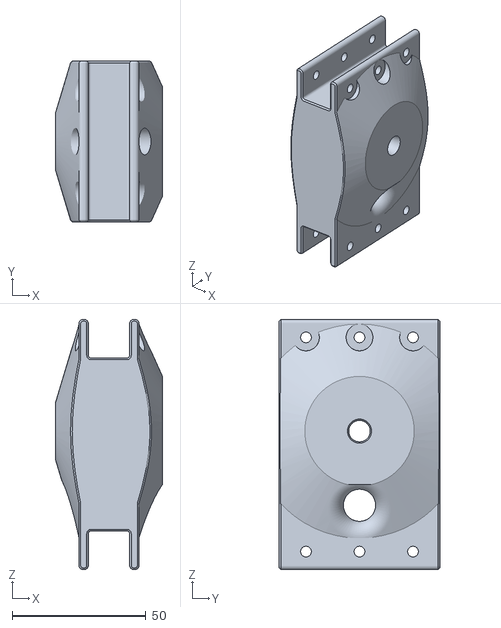
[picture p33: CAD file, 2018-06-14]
STL/Rocker Body Mount.stl
40.0 x 60.0 x 93.4

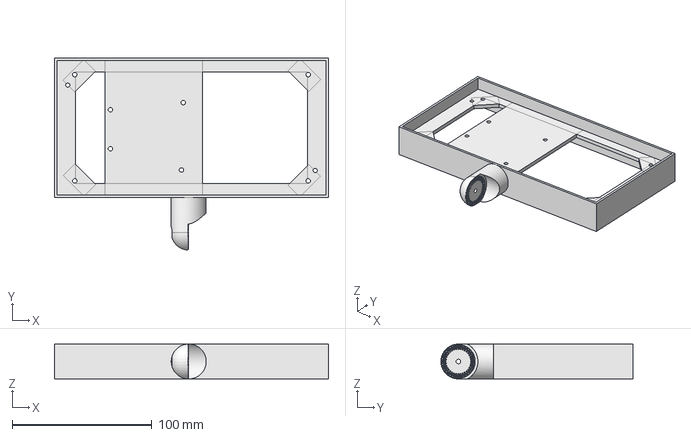
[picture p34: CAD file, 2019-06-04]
modifications/Marco_Walther/DisplayTop.FCStd
196.0 x 137.5 x 25.0 mm

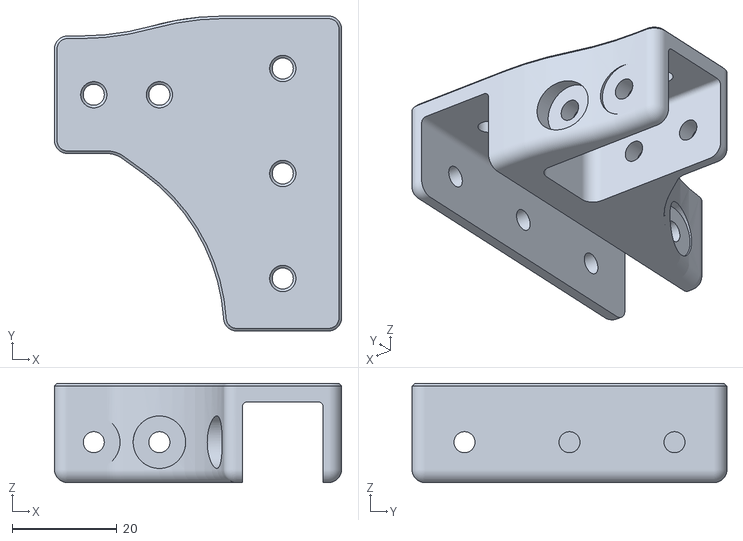
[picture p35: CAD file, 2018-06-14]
STL/DiffEnd.stl
54.7 x 60.0 x 18.9

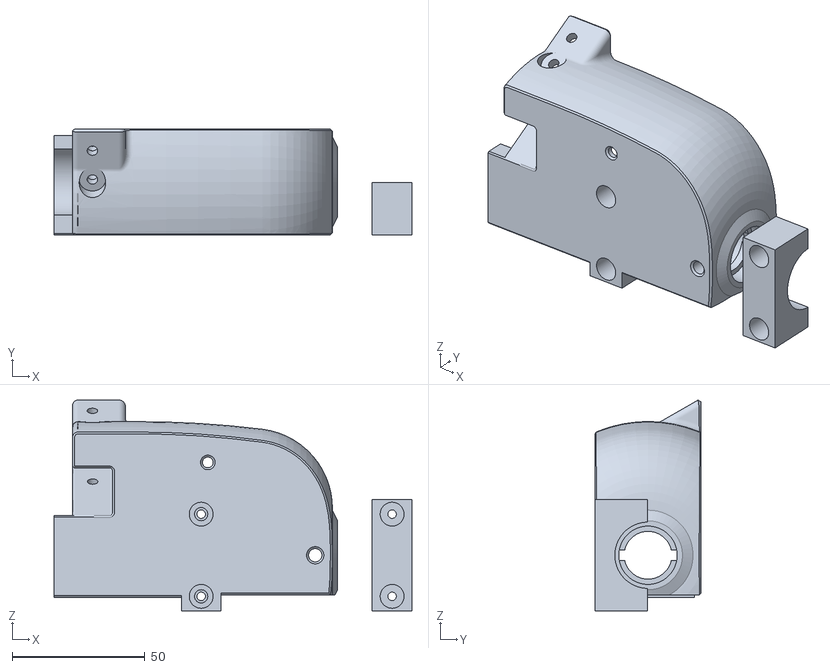
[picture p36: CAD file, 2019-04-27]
modifications/Marco_Walther/Fixed Knuckle 25D.stl
135.0 x 40.0 x 79.5

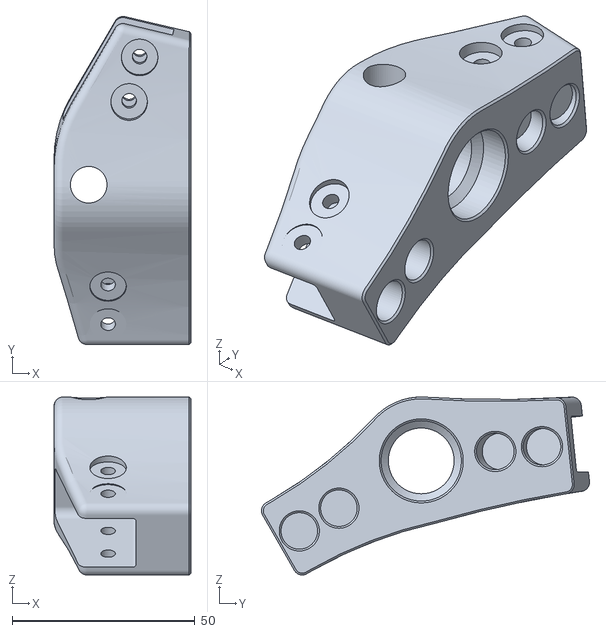
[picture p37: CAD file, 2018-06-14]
STL/Bogie-Wheels.stl
37.5 x 89.8 x 48.7

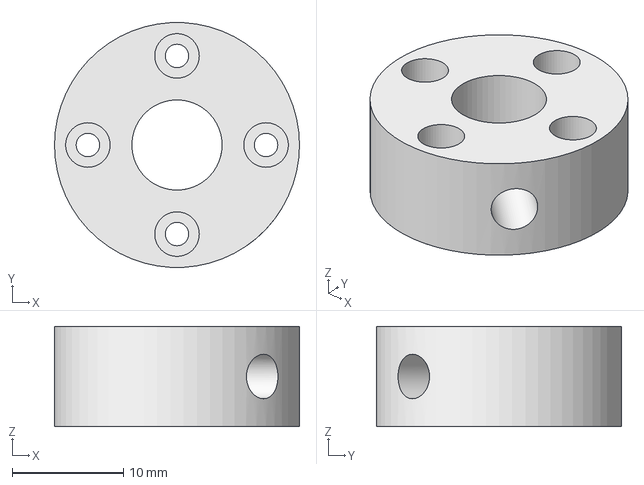
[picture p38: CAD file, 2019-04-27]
modifications/Marco_Walther/AX-12-Coupler.fcstd
22.0 x 22.0 x 9.00 mm

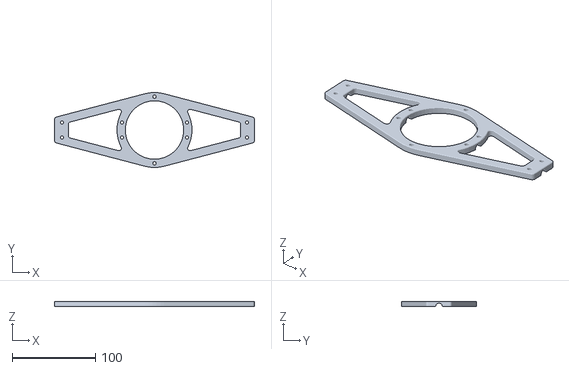
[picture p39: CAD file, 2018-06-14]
STL/DiffBrace.stl
240.0 x 89.9 x 6.00

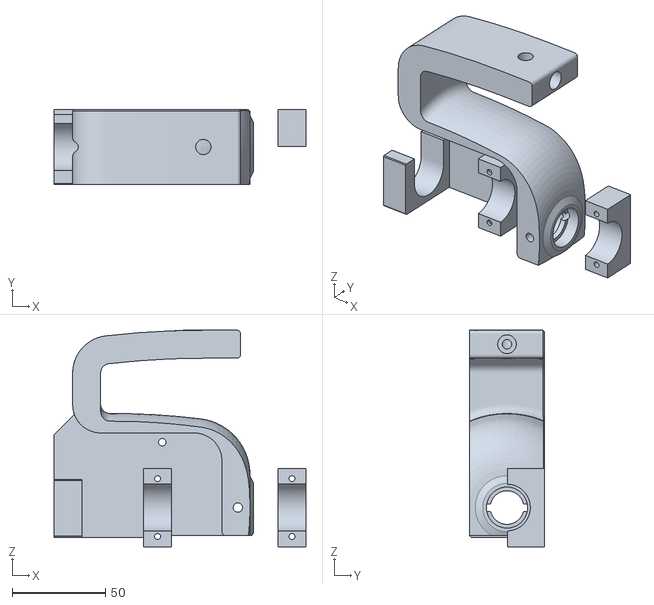
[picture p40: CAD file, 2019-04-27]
modifications/Marco_Walther/Steering Knuckle 25D.stl
135.0 x 40.0 x 116.0

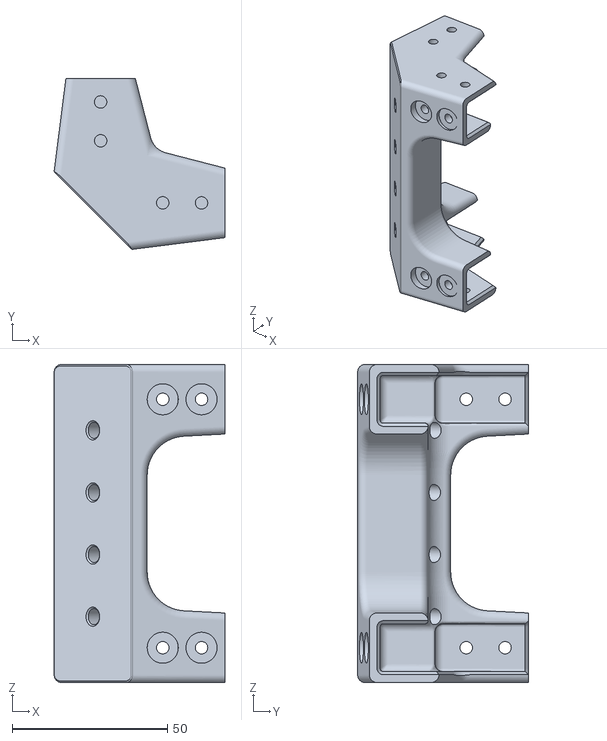
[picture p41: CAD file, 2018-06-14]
STL/Body Corner.stl
55.0 x 55.0 x 102.4

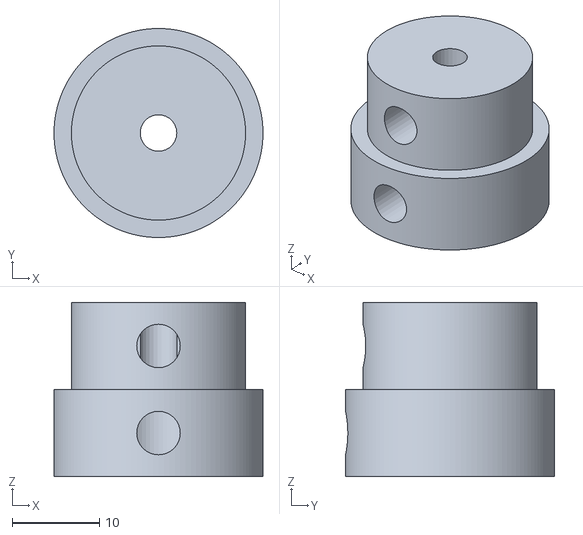
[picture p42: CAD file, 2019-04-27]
modifications/Marco_Walther/25D Coupler.stl
24.0 x 24.0 x 20.0

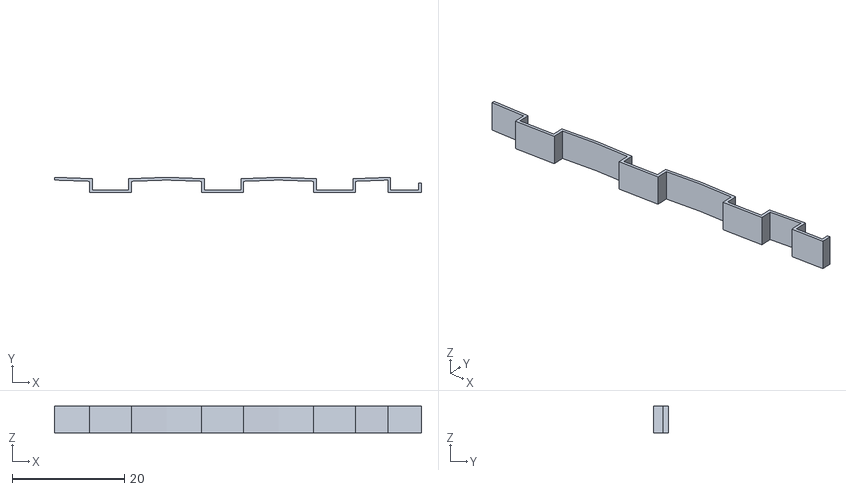
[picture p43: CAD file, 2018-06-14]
STL/Clip3n20.stl
65.5 x 2.75 x 4.80

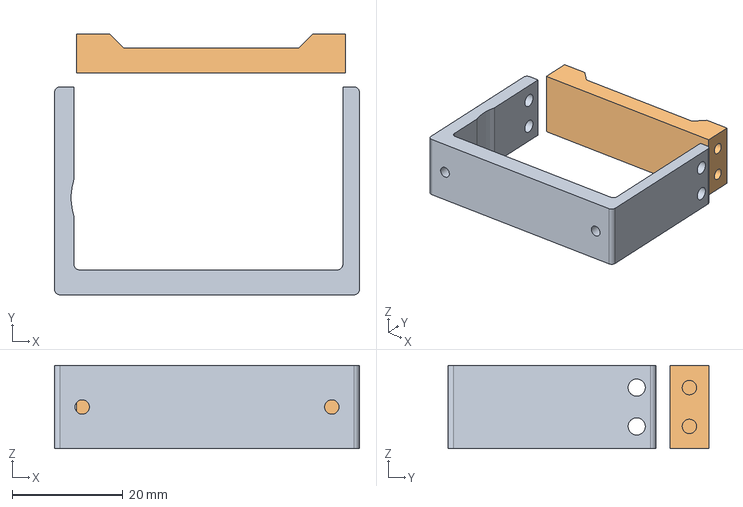
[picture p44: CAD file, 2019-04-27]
modifications/Marco_Walther/AX-12-Bracket.fcstd
55.0 x 47.0 x 15.0 mm

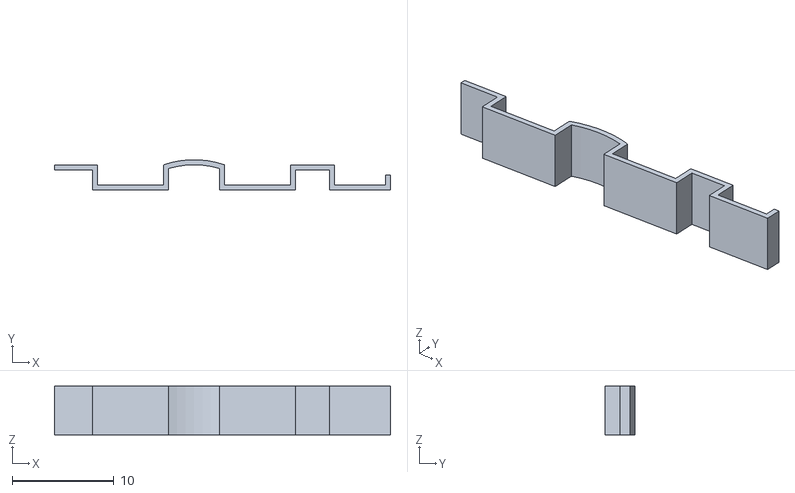
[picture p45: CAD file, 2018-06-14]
STL/Clip2n125.stl
33.1 x 2.99 x 4.80

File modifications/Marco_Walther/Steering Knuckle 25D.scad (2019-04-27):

$fa = 3;
$fs = .5;

module clamp() {
    difference() {
        translate([0, -20, -21]) {
            cube(size = [15, 19.75, 42]);
        }
        rotate([0, 90, 0]) {
            cylinder(h = 20, r = 12.5);
        }
    }
}

module k() {
    difference() {
        union() {
            import("Steering Knuckle.stl");
            translate([-80, 17.5, -16]) {
                cube(size = [50, 2.5, 55]);
            }

            translate([-80, 17.5, 39]) {
                rotate([0, 45, 0]) {
                    cube(size = [25, 2.5, 18]);
                }
            }


            translate([-80, -20, -16]) {
                cube(size = [15, 37.5, 31]);
            }

            translate([-32, 0, 0]) {
                rotate([180, 0, 0]) {
                    clamp();
                }
            }
        }
        translate([-80, 0, 0]) {
            rotate([0, 90, 0]) {
                cylinder(h = 20, r = 12.5);
            }
        }
        translate ([-80, -12.5, 0]) {
            cube(size = [20 , 25, 15]);
        }
        translate([-81, -20, -18]) {
            rotate([45, 0, 0]) {
                cube(size = [49, 2, 2]);
            }
        }
       translate([-85, -20.5, 14]) {
            rotate([45, 0, 0]) {
                cube(size = [20, 2, 2]);
            }
        }
    }
}
 

//        translate([-32, -13, -14]) {
//            difference() {
//                rotate([0, 90, 0]) {
//                    cylinder(h = 15, r = 7);
//                }
//                translate([-1, 0, -7]) {
//                    cube(size = [17, 14, 14]);
//                }
//                translate([-1, -7, 0]) {
//                    cube(size = [17, 14, 14]);
//                }
//            }
//        }
        

module h() {
    union() {
        rotate([90, 0, 0]) {
            cylinder(h = 30, r = 1.6);
        }
        translate([0, -2, 0]) {
            rotate([90, 0, 0]) {
                cylinder(h = 28, r = 2.5);
            }
        }
        translate([0, -9, 0]) {
            rotate([90, 0, 0]) {
                cylinder(h = 21, r = 4.5);
            }
        }
    }
}

module h1() {
    union() {
        rotate([90, 0, 0]) {
            cylinder(h = 30, r = 1.6);
        }
        translate([0, -7, 0]) {
            rotate([90, 0, 0]) {
                cylinder(h = 23, r = 4.5);
            }
        }
    }
}


difference() {
    k();
    rotate([180, 0, 0]) {
        translate([-24.5, 0, -15.5]) {
            h();
        }
    }
    rotate([180, 0, 0]) {
        translate([-24.5, 0, 15.5]) {
            h();
        }
    }
}

rotate([180, 0, 0]) {
    translate([40, 0, 0]) {
        difference() {
            clamp();
            translate([7.5, 0, -15.5]) {
                h1();
            }
            translate([7.5, 0, 15.5]) {
                h1();
            }
        }
    }
}
// color("red") {
//    translate([-76, 0, 0]) {
//        rotate([0, 90, 0]) {
//            cylinder(h = 75, r = 12.5);
//        }
//    }
//}

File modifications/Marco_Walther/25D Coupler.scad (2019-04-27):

$fa = 3;
$fs = .5;

union() {
    difference() {
        cylinder(h = 10, r = 12);
        cylinder(h = 10, r = 4.1);
        translate([0, 0, 5]) {
            rotate([90, 0, 0]) {
                cylinder(h = 15, r = 2.5);
            }
        }
    }

    translate([0, 0, 10]) {
        difference() {
            cylinder(h = 10, r = 10);
            cylinder(h = 10, r = 2.1);
            translate([0, 0, 5]) {
                rotate([90, 0, 0]) {
                    cylinder(h = 15, r = 2.5);
                }
            }
        }
    }
}

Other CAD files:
STL/Rocker.stl
STL/LX-16A - Bracket.stl
STL/LX-16A - Coupler.stl
STL/Steering Knuckle.stl
modifications/Marco_Walther/Fixed Knuckle 25D.scad
STL/Battery Tray.stl
STL/Bogie-Body.stl
STL/DiffLink.stl
STL/DiffLower.stl
STL/DiffUpper.stl
STL/Fixed Knuckle.stl
STL/Front Corner.stl
STL/Power Panel.stl
STL/Rear Corner.stl
STL/Rod Support.stl
STL/Wheel Hub.stl
STL/Wheel.stl
modifications/Marco_Walther/AX-12-Bracket.stl
modifications/Marco_Walther/AX-12-Coupler.stl
modifications/Marco_Walther/DisplayBottom.stl
modifications/Marco_Walther/DisplayTop.stl

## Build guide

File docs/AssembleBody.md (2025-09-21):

# Body Assembly

These parts make up the box that serves as the rover's main body and equipment bay.

**Estimated Time:** 1 hour 15 minutes

**Parts:**
* 4 * [Printed corner pieces](Print%20Body%20Box%20Corners.md)
* 4 * [385mm extrusion beams](Misumi%20HFS%203.md)
* 4 * [245mm extrusion beams](Misumi%20HFS%203.md)
* 2 * [Rocker joint body mount](AssemblePivotJoints.md)
* 12 * [Installation tool for 3 M3 nuts, 20mm apart](Print%20M3%20Installation%20Tool.md)
* 32 * [Installation tool for 2 M3 nuts, 12.5mm apart](Print%20M3%20Installation%20Tool.md)
* 100 * M3x8mm bolts
* 100 * M3 washers

***If using mast mount***
* 2 * [Installation tool for 2 M3 nuts, 12.5mm apart](Print%20M3%20Installation%20Tool.md)
* 4 * M3 washers

***If using power tray***
* 4 * [Installation tool for 2 M3 nuts, 12.5mm apart](Print%20M3%20Installation%20Tool.md)
* 4 * M3 washers

***If using bottom plate***
* 14 * [Installation tool for 2 M3 nuts, 12.5mm apart](Print%20M3%20Installation%20Tool.md)
* 28 * M3 washers

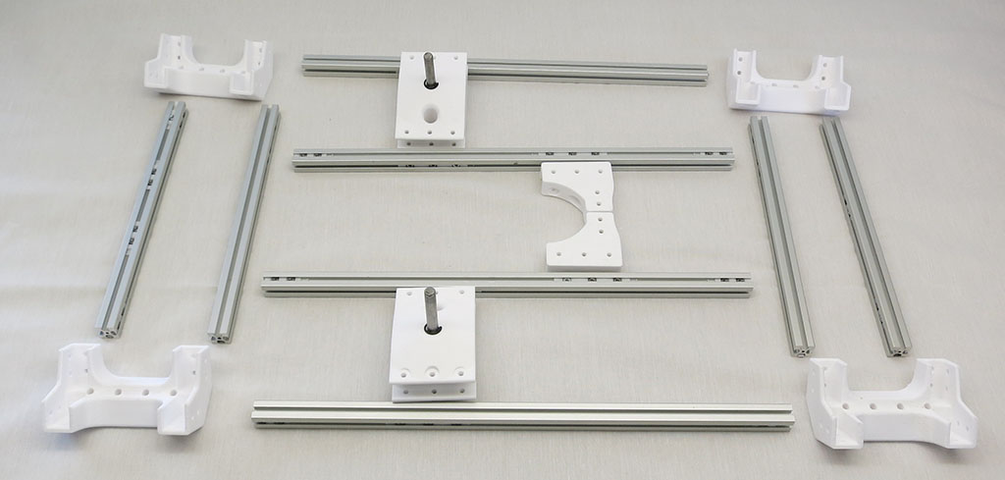
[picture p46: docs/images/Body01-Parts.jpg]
Body parts


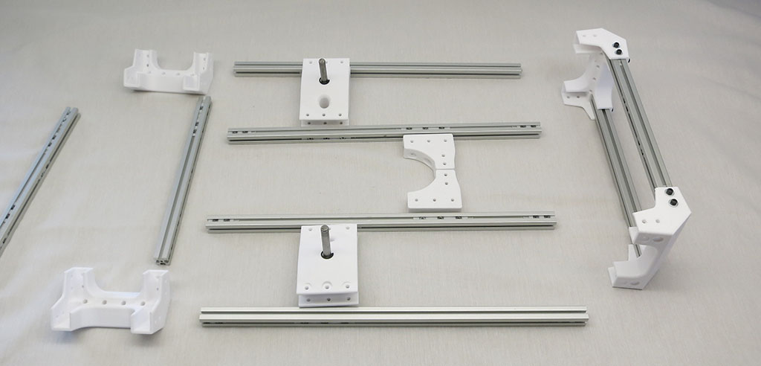
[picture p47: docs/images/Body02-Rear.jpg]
Body rear


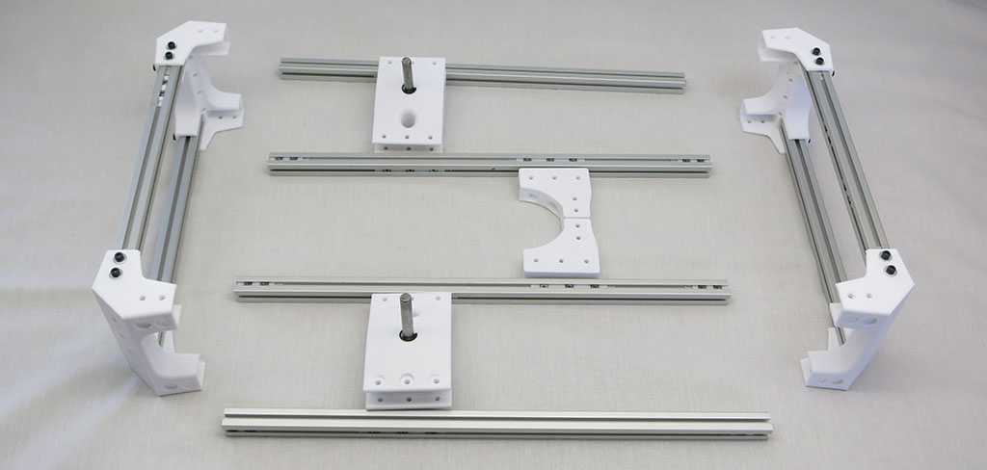
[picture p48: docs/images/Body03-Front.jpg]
Body front


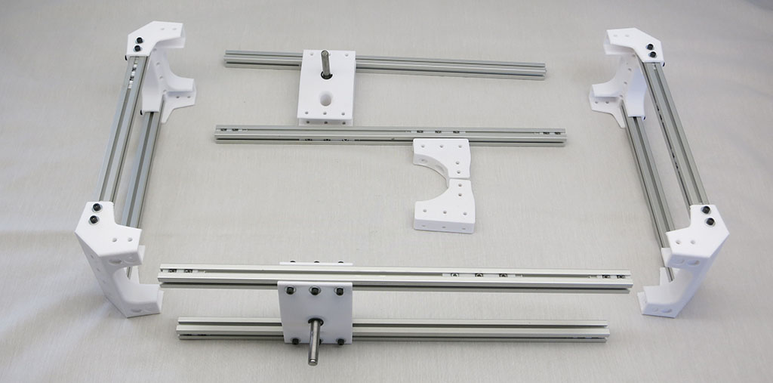
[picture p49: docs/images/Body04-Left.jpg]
Body left


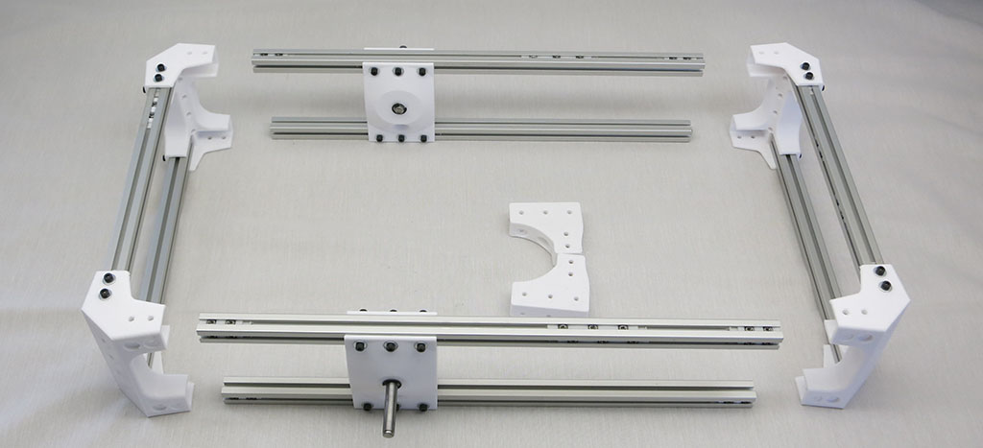
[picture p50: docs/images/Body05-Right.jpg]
Body right


**Note:** Before attaching the rear body portion to the body sides, the last 4 of the [Installation tools for 3 M3 nuts, 20mm apart](Print%20M3%20Installation%20Tool.md) should be installed in the top beam of the right and left body sides for future installation of the [Differential End Pieces](../STL/DiffEnd.stl) during the [Suspension Differential Assembly](AssembleDifferential.md). They are installed in the top and outside slots of the top beams.
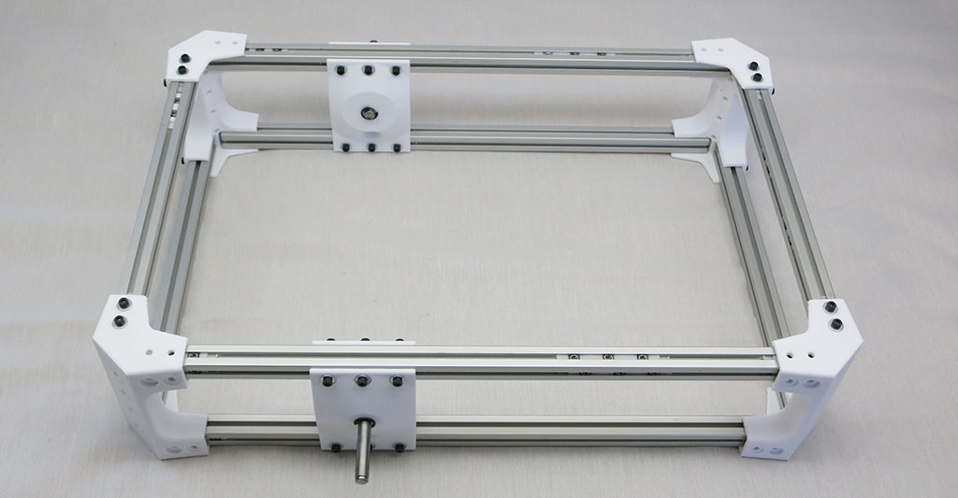
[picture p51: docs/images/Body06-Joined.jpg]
Body joined


For proportion faithful to Curiosity rover side view seen in Onshape CAD file, there should be 62mm of aluminum extrusion visible between front face of "Rocker Body mount" and rear face of front "Body Corner".

In practice this can be moved forward/back as the builder pleases to maintain best balance for their rover chassis. Which will vary with every rover build as it depends on what's installed in equipment bay.

---

Here are more details on fasteners and their associated installation clips, contributed by
[knickels](https://github.com/NickelsLab)

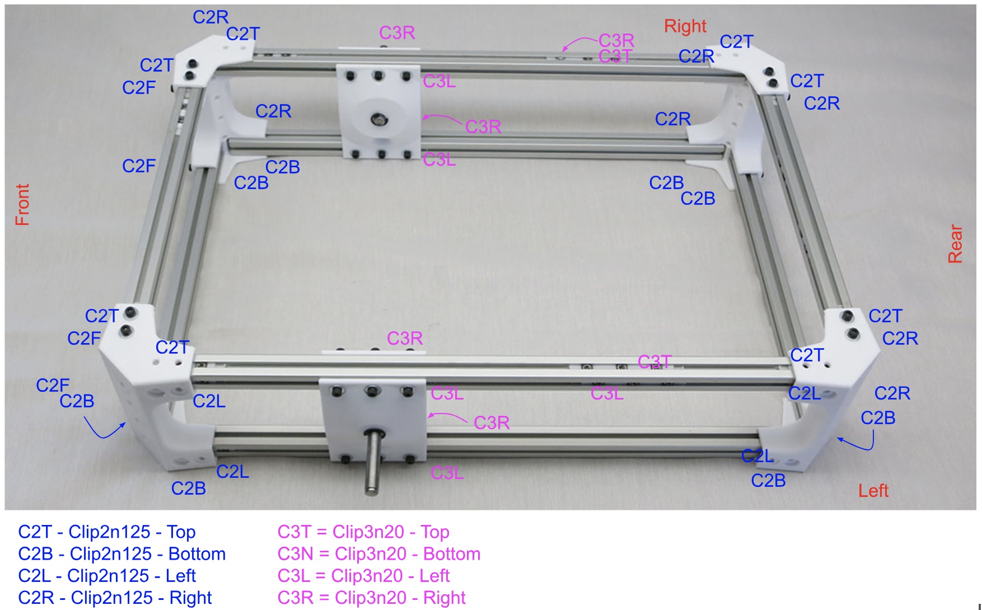
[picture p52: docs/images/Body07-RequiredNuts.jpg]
Required Nuts


Once you assemble the body, you don't have easy access to slide more nuts into the slots, so you need to decide now if you will want the option to add some accessories to the rover.

**Bottom Plate:** If you will be installing the bottom plate, you will need 14 more of [Installation tool for 2 M3 nuts, 12.5mm apart](Print%20M3%20Installation%20Tool.md), installed on the bottom slots, with 3 on the short ends and 4 on the long ends.
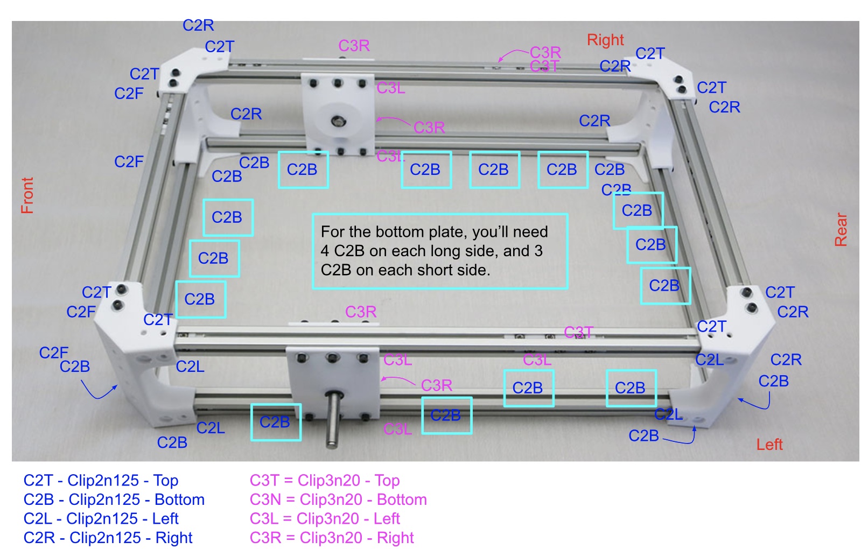
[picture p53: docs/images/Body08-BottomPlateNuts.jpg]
Bottom Plate Nuts


**Mast:** If you will be installing the mast, you will need 2 more of [Installation tool for 2 M3 nuts, 12.5mm apart](Print%20M3%20Installation%20Tool.md), installed on the top front right corner.
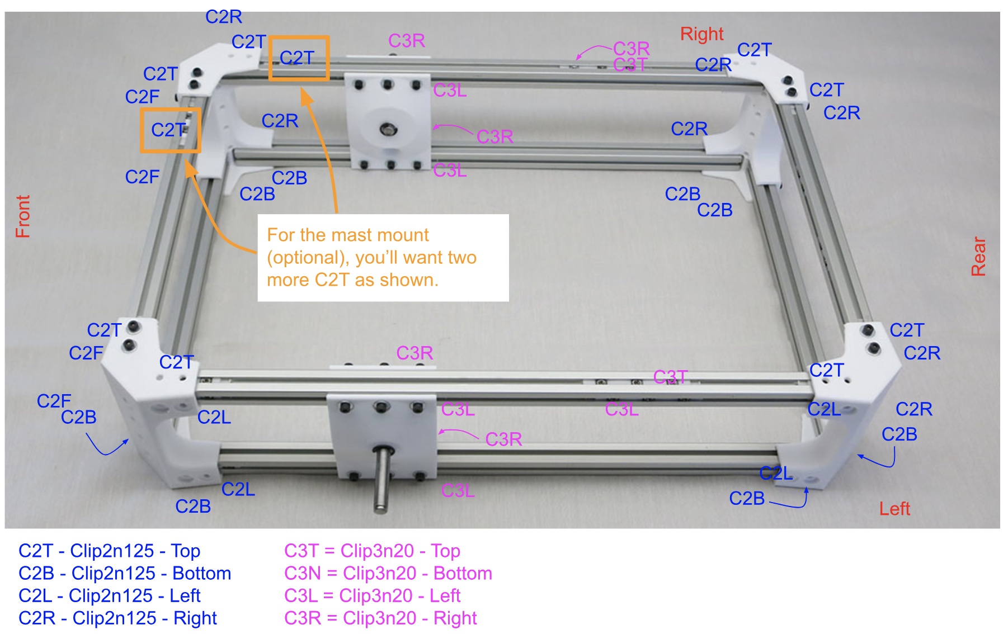
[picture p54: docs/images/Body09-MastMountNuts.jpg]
Mast Mount Nuts


**Power Tray:** If you will be installing the power tray, you will need 4 more of [Installation tool for 2 M3 nuts, 12.5mm apart](Print%20M3%20Installation%20Tool.md), with two installed on the front of the rear top short beam, and two installed on the rear of the rear bottom short beam.
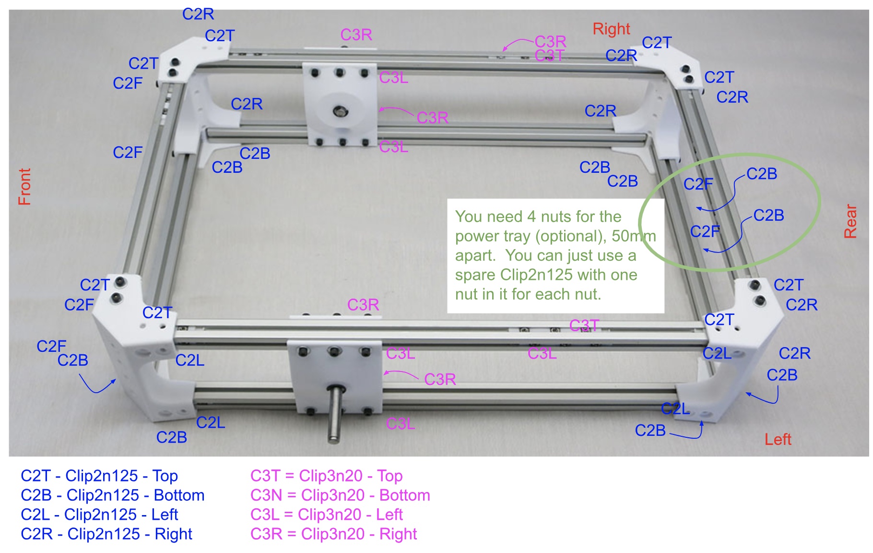
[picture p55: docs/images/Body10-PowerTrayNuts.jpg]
Power Tray Nuts


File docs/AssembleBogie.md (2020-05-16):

# Bogie Assembly

Bogie portion of the suspension links the middle wheel to the rear wheel.

**Estimated Time:** 30 minutes per side = 1 hour total

**Parts:**
* 1 * [117mm aluminum beam](Misumi%20HFS%203.md)
* 1 * [122mm aluminum beam](Misumi%20HFS%203.md)
* 1 * [Rear steering corner](Print%20Corner%20Steering%20Joints.md#rear-corners)
* 1 * [Fixed knuckle](Print%20Fixed%20Knuckle.md)
* 1 * [Bogie pivot](Print%20Suspension%20Bogie%20Joints.md#bogie-pivot)
* 1 * [Steering knuckle](Print%20Steering%20Knuckle.md)
* 1 * [Servo actuator module](AssembleActuatorModule.md)
* 11 * [M3 nut installation tool for 2 nuts, 12.5mm apart](Print%20M3%20Installation%20Tool.md)
* 2 * M3 set screws
* 24 * M3x8mm bolts
* 24 * M3 washers

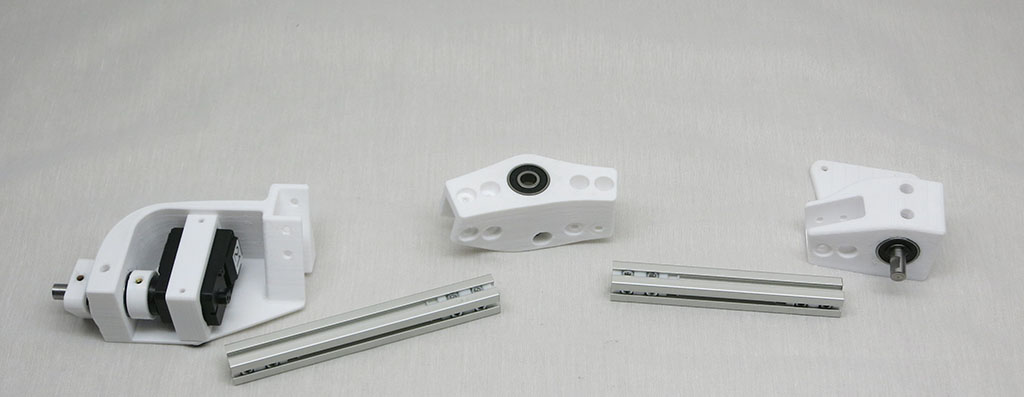
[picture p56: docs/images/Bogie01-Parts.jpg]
Bogie parts


The 117mm extrusion connects the Rear Corner and the angled side of the Bogie Wheel part.

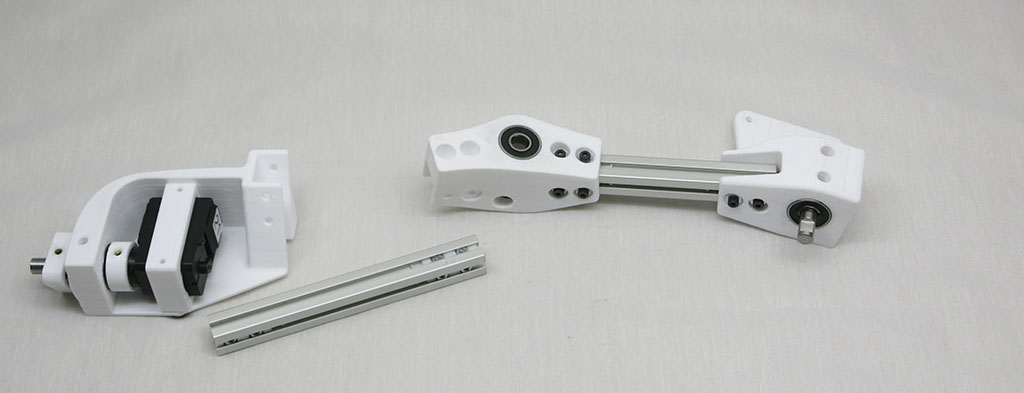
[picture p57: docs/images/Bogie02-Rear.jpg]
Bogie rear installed


The 122mm extrusion connects the Bogie Wheel part on the straight side, and the Fixed Knuckle. The extrusion extends from the open side of the Fixed knuckle.

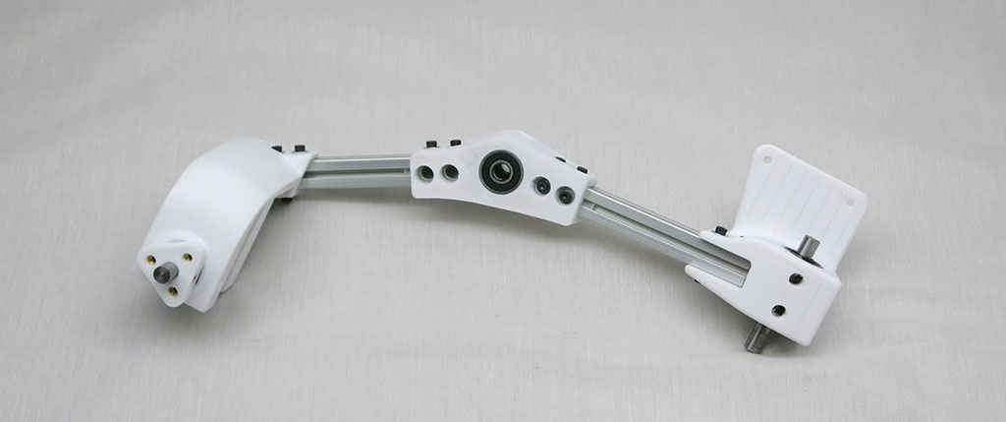
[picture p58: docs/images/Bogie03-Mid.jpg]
Bogie mid installed


The Rear Corner should extend out away from the body when the assembly is mounted.

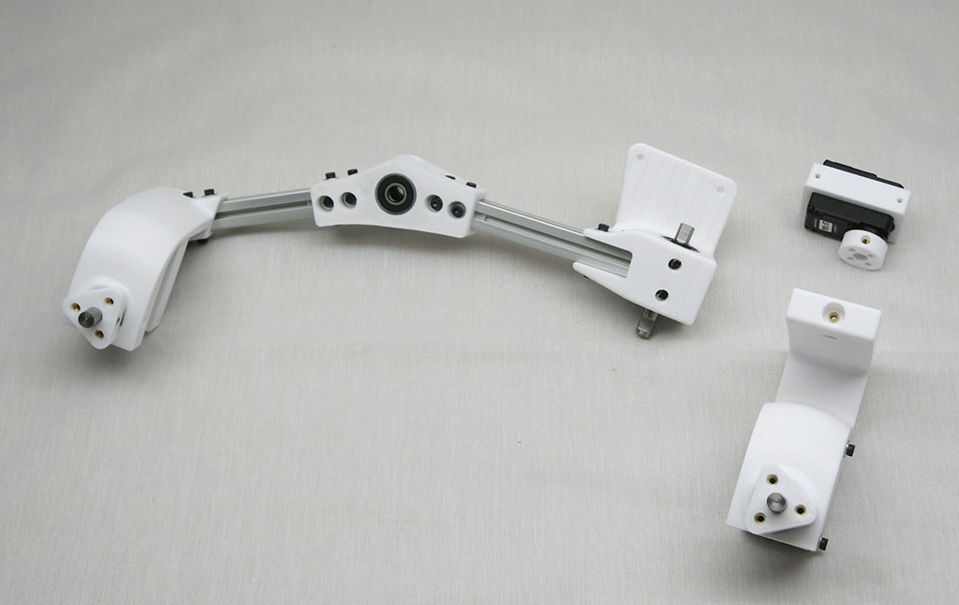
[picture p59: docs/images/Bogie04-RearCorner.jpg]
Bogie with rear corner components


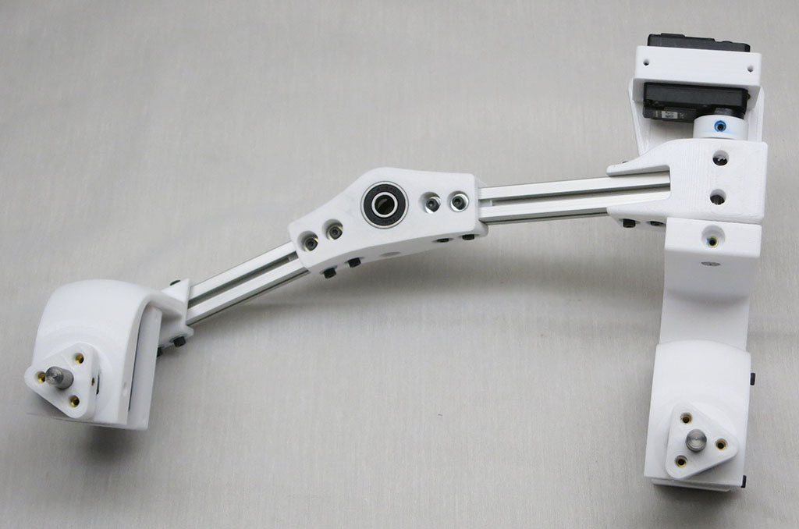
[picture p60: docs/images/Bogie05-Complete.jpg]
Bogie complete


Repeat for other side of rover.

## Sawppy V1 Errata
Sawppy v1 has a design flaw where it is easy to make the mistake of using the
left side Bogie-Wheel part on the right side of the rover. (And vice-versa.) Several
rover builders were caught by this, and I am contemplating several ways to improve. In the
meantime please be aware: If a Sawppy rover's two middle wheels are splayed out
rather than parallel with each other and aligned with the body, it is because their
Bogie-Wheel parts had been installed left-right reversed from intended. (Thanks to
[Tim](https://hackaday.io/timing2211) for sharing these pictures.)

Correct | Bogie-Wheel part reversed left-right
--- | ---
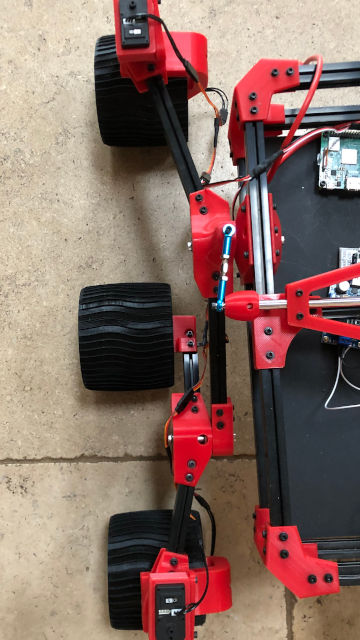
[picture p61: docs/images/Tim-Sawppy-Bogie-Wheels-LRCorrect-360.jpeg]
Correct Bogie-Wheel installation
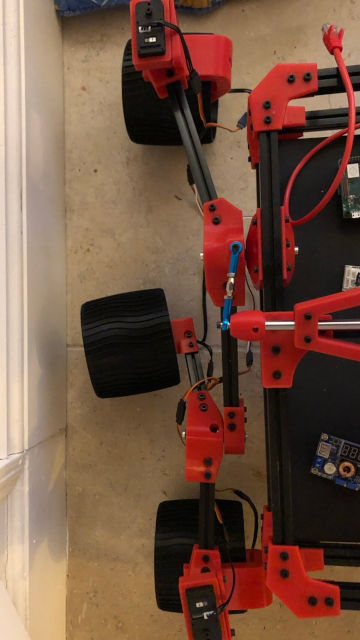
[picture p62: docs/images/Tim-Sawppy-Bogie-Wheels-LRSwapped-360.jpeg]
Left-right reversed Bogie-Wheel installation
 | 
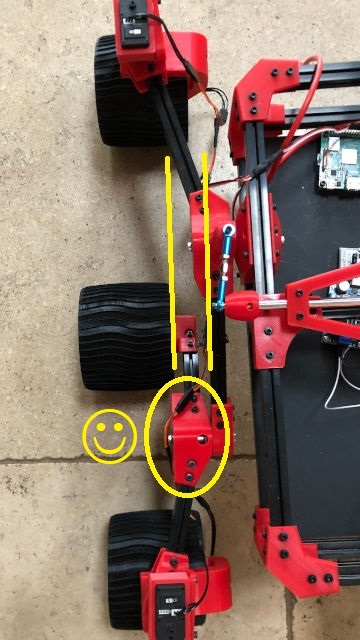
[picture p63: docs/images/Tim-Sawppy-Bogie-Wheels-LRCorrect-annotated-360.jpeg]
Correct Bogie-Wheel installation annotated
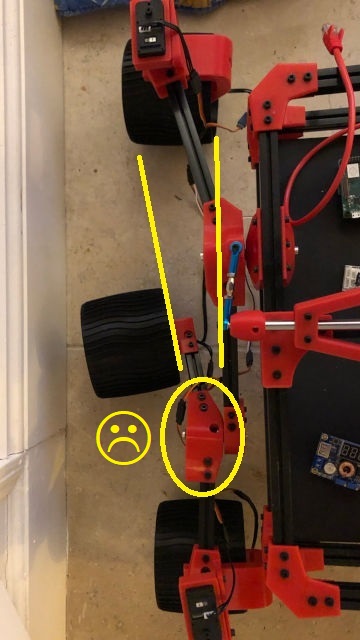
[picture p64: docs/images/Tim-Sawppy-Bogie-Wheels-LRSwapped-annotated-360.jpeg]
Left-right reversed Bogie-Wheel installation annotated
 |

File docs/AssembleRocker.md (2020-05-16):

# Rocker Assembly

Rocker portion of suspension arm links the front wheel to the bogie assembly.
The whole suspension subassembly is then mounted to the main body box.

**Estimated Time:** 30 minutes each * 2 sides = 1 hour total

**Parts:**
* 1 * [161mm aluminum beam](Misumi%20HFS%203.md)
* 1 * [182mm aluminum beam](Misumi%20HFS%203.md)
* 1 * [Bogie fixed end](Print%20Suspension%20Bogie%20Joints.md#bogie-fixed)
* 1 * [Front steering corner](Print%20Corner%20Steering%20Joints.md#front-corners)
* 1 * [Rocker print](Print%20Suspension%20Rocker%20Joints.md#rocker)
* 1 * [Steering knuckle](Print%20Steering%20Knuckle.md)
* 1 * [Servo actuator module](AssembleActuatorModule.md)
* 1 * [Bogie assembly](AssembleBogie.md)
* 12 * [M3 nut installation tool for 2 nuts, 12.5mm apart](Print%20M3%20Installation%20Tool.md)
* 2 * M3 set screws
* 26 * M3x8mm bolts
* 2 * M3x16mm bolts
* 26 * M3 washers
* 2 * Retaining E-clips
* 1 * Turnbuckles

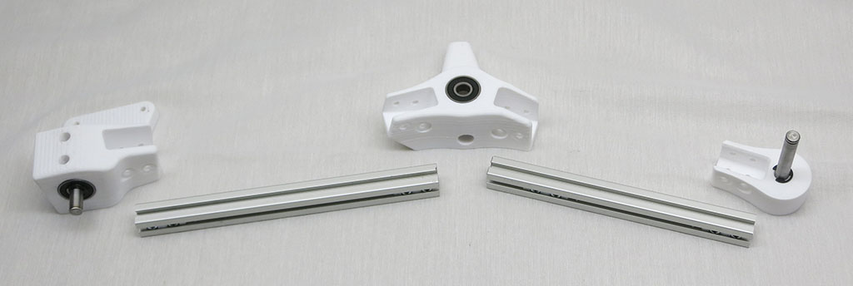
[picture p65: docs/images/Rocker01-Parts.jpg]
Rocker parts


Aluminum beam to link to bogie. The 161mm extrusion goes between the Bogie End and the straight side of the Rocker.

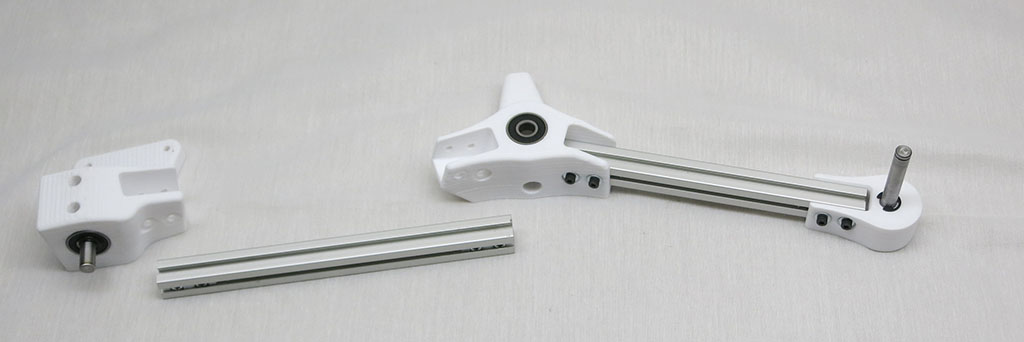
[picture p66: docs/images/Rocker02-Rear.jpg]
Rocker link to bogie


Aluminum beam to link to front corner. The 182mm extrusion goes between the angled side of the Rocker and the Front Corner.

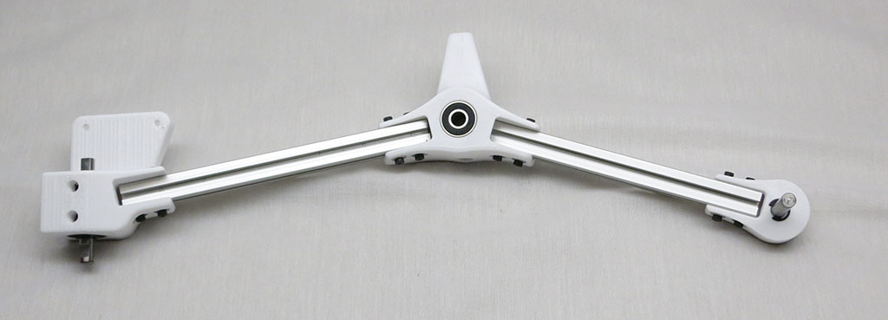
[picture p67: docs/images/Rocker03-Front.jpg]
Rocker link to front wheel


Front corner steering mechanisms.

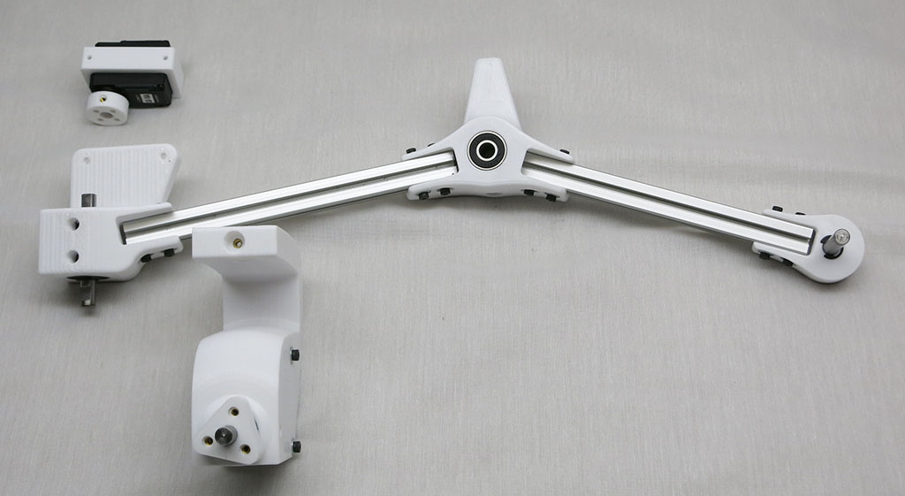
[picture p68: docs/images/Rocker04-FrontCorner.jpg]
Front corner steering pieces


Rocker subassembly complete.

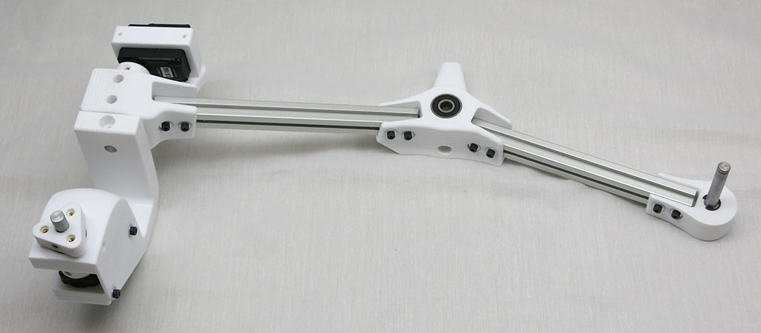
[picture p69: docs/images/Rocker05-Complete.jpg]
Rocker complete


Rocker subassembly attached to bogie subassembly via E-clip. The three wheel mounts should all be roughly in line with each other, with the center wheel extending slightly farther away from the body than the corner wheels. If the center wheel is splayed outward at an angle, the Bogie Wheel part has been swapped side to side. See "Sawppy V1 Errata" at the end of the
[bogie assembly page](AssembleBogie.md)

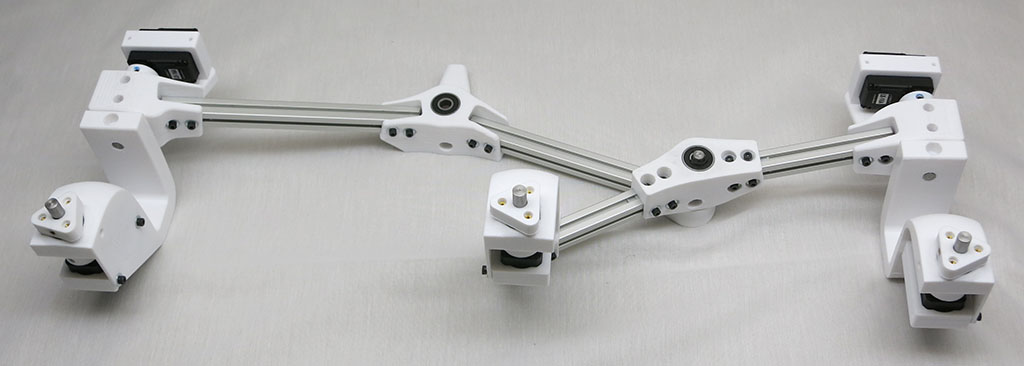
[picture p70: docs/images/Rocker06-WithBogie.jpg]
Join up with bogie


Rocker-bogie installed on body via E-clip.

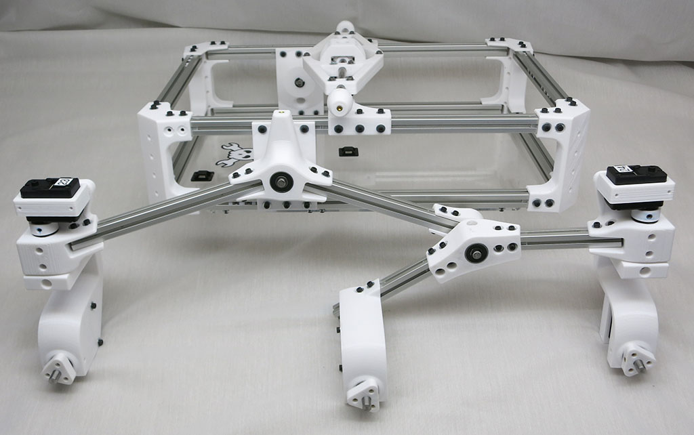
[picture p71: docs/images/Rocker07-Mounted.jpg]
Join up with body


Rocker-bogie connects to differential via turnbuckle. M3x16mm bolts without washers are used for attaching the turnbuckles.

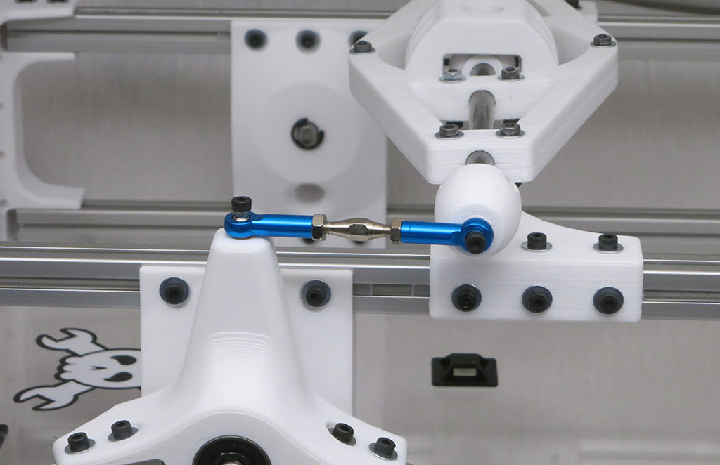
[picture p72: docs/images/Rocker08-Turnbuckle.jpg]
Turnbuckle connects to differential


Repeat for other side of body.

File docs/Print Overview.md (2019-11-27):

# 3D Printing Overview

Some general information about 3D printing Sawppy the Rover's parts

All of the 3D-printed parts were designed to be tolerant of dimensional errors. A less fancy way
to rephrase is: you don't need an expensive high precision 3D printer to print this rover.
In order to verify this claim, I purchased one of the least expensive 3D printers available
and printed an entire iteration of the rover on it.

## Verified to be Printable On Monoprice Maker Select

I bought a [Monoprice Maker Select](https://www.monoprice.com/product?p_id=13860), which is a rebranded
[Wanhao Duplicator i3](http://www.wanhao3dprinter.com/Unboxin/ShowArticle.asp?ArticleID=70), which is
itself a knockoff of the [Prusa i3](https://www.prusaprinters.org/prusa-i3/).
And not even a new one - I bought a returned "[Open Box](https://www.monoprice.com/product?p_id=21864)"
unit which is occasionally on sale for $199 or less. The downside, of course, is the printer will show
signs of (ab)use by its previous owner. The condition will be the luck of the draw.

This printer has a print bed 200mm wide by 200mm deep and roughly 180mm tall which can
comfortably print any single rover part. (It's actually large enough to print several parts at once.)
Most rover parts can in theory fit within the 120mm x 120mm area of the
[Monoprice Maker Select Mini](https://www.monoprice.com/product?p_id=15365)
(or [open box](https://www.monoprice.com/product?p_id=30386)) but a few large parts (like the differential
brace) will not fit and some parts (like the wheel) will be a very tight fit.

All that said, if you want to print this rover on a Monoprice Maker Select/Wanhao Duplicator i3,
know that its low price does come with tradeoffs.

### Known Problems Printing on Monoprice Maker Select/Wanhao Duplicator i3

* The printer chassis is not very rigid. In practice, this translates to minor surface distortions.
Surfaces that are supposed to be flat become a little wavy, things of that nature. Fortunately these
cosmetic flaws are irrelevant for rover operation.
* It is not a heavy duty piece of equipment and may break down under continuous use. Either plan on
letting the machine rest between print jobs, or plan on making printer upgrades. It is a popular
enough printer that an internet search will help you do whatever you need to do to with this printer.
I chose the upgrade path when the default control board started emitting the smell of unhappy
electronics after a few weeks of around-the-clock printing. The stock control board was replaced with
an [Azteeg X5 mini](http://www.panucatt.com/azteeg_X5_mini_reprap_3d_printer_controller_p/ax5mini.htm).
* The first draft of the rover was printed in PLA, the second in PETG. While the stock print head for
the Monoprice Maker Select is technically capable of PETG, it could only reliable extrude at a very
slow rate. In order to speed up printing PETG the stock print hardware must be upgraded to an all-metal
hot end, in my case an [E3D Titan Aero](https://e3d-online.com/titan-aero).

## STL Orientation

All STL posted to Github were exported from Onshape CAD in medium resolution
and retained their X/Y/Z orientation in 3D CAD space. Most pieces can be
easily reoriented to place them properly on the print bed. However, the front
and rear suspension corner pieces can be tricky with their odd angle. When
possible, use your slicer's function to orient a model to print bed.

* Simplify3D: Edit/[Place Surface on Bed](https://www.simplify3d.com/support/articles/importing-and-manipulating-your-models/) (Ctrl-L)
* Slic3r Prusa Edition: [Place on Face](https://twitter.com/josefprusa/status/1033719313751044096)
* Cura: [Lay flat](https://ultimaker.com/en/resources/16583-adjusting-the-model)
* MatterControl: [Lay flat](https://www.matterhackers.com/articles/mattercontrol-design-tools)

If your slicer software does not have similar functionality, use
[Meshmixer](http://www.meshmixer.com/) to reorient STL. Here is [one tutorial](https://mattshub.com/2018/02/24/orientating-parts-in-meshmixer/)
out of many available online to guide through the process.

## STL Slicer Settings

The rover prototypes were printed with the following parameters:

* Nozzle Diameter: 0.4mm (default nozzle of Monoprice Maker Select)
* Layer Height: 0.3mm
* Number of perimeters: 3. (Multiplied by 0.4mm nozzle diameter equals 1.2 mm vertical walls.)
* Number of top/bottom layers: 4. (Multiplied by 0.3mm layer height equals 1.2mm horizontal walls.)
* Infill type: Triangular
* Infill percentage: 30%

The first draft was printed in PLA at high speed for fast iteration, at the sacrifice of some
precision. The second was in PETG and printed slower because of the nature of PETG and it also
gave us more precise dimensions.

All parts were designed to be printed without supports.

## Print post-processing

In addition to the typical cleanup work required of 3D printed parts, some printed rover parts require
post-processing of the following types:

* **Bridge Removal**: All bolt holes facing the print bed will have a thin layer of extra plastic to
help the 3D printer bridge across what would otherwise be empty space for the bolt hole. After printing
is complete, this thin layer can be removed with a drill bit diameter around 4mm or 5/32". Smaller is
OK, precision is not as important in bridge removal.
* **Reaming**: Several pieces need to precisely fit around an 8mm steel shaft. A reamer is a precise cutting tool
to ensure the printed 8mm hole will fit an 8mm shaft. An 8mm drill bit is not as good. Precision matters
here, and a 5/16" drill bit (which is technically closer to 7.93mm) may not be good enough.
* **Tapping**: A few parts are not mechanically demanding, so we can tap M3 thread directly
into the plastic.
* **Heat-set thread insert**: The rest of the parts that use M3 fasteners will need a brass heat-set
insert installed in the plastic for a durable M3 thread.
* **608 Bearings**: Sawppy the Rover uses [commodity type 608 bearings](https://newscrewdriver.com/2018/03/07/for-cheap-commodity-bearings-search-for-608/)
held in printed plastic parts. If the 22mm hole is a little too small, the bearings will need to be
installed with the help of a tool. Ideally an [arbor press](https://en.wikipedia.org/wiki/Arbor_press), but a C-clamp will work.

## Cost estimate

Precise cost will depend on printer settings and filament choice, but should be in the range of $50-$75.

Sawppy's design iterated through parts printed with [inexpensive PLA](https://www.monoprice.com/product?p_id=10552). Once version 1.0 was finalized, all parts were reprinted in PETG. This consumed roughly 2.5 spools of 1 kilogram [PETG](https://www.matterhackers.com/store/l/petg-white-high-strength-filament-1.75mm/sk/M1VF5877)

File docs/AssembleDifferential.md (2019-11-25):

# Differential Assembly

The differential pivots about the center of the rover body to distribute suspension motion across
to the other side of the rover.

**Estimated Time:** 45 minutes

**Parts:**
* All [printed differential components](Print%20Differential.md)
* 1 * 8mm diameter 300mm long steel shaft
* 1 * [238mm aluminum beam](Misumi%20HFS%203.md)
* 8 * [M3 nut installation tool for 2 nuts, 12.5mm apart](Print%20M3%20Installation%20Tool.md)
* 32 * M3x8mm bolts
* 10 * M3x16mm bolts
* 26 * M3 nuts
* 52 * M3 washers
* 2 * M3 set screws

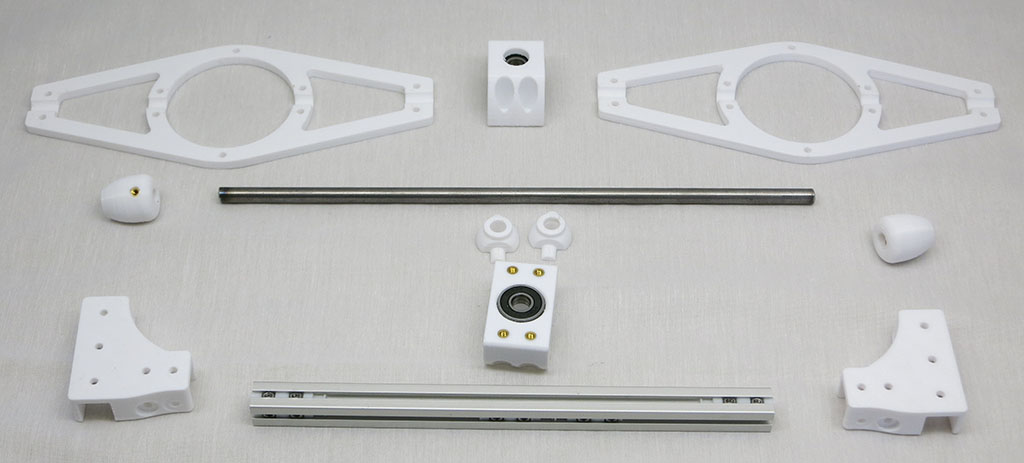
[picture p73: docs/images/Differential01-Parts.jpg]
Differential parts


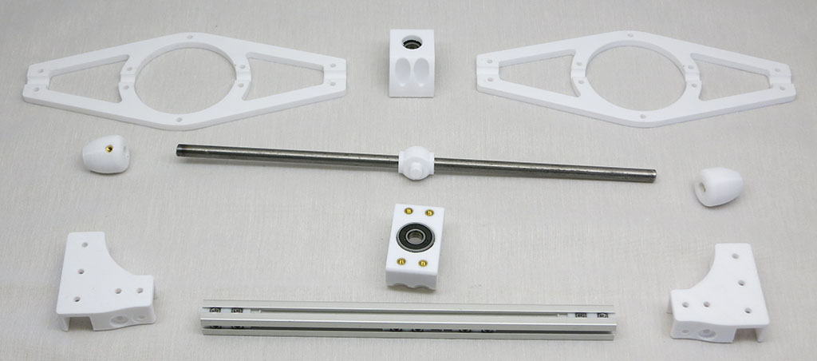
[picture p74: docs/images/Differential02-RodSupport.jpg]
Differential rod support installed


Use 4 M3x8mm bolts with washers to fasten upper and lower parts of differential pivot.

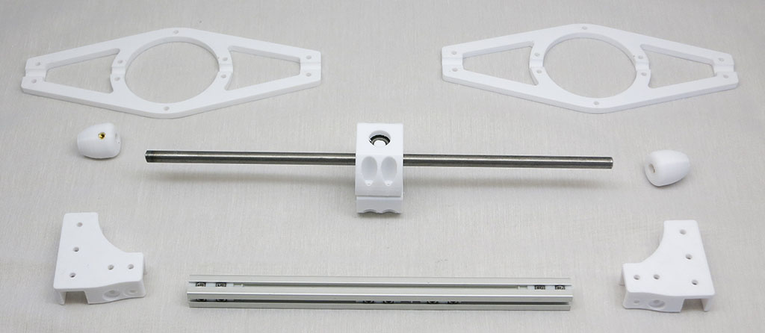
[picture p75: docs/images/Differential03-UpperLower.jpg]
Upper and lower part of differential installed


Use 10 M3x16mm bolts and nuts (with washers) to fasten top and bottom parts of differential brace together.

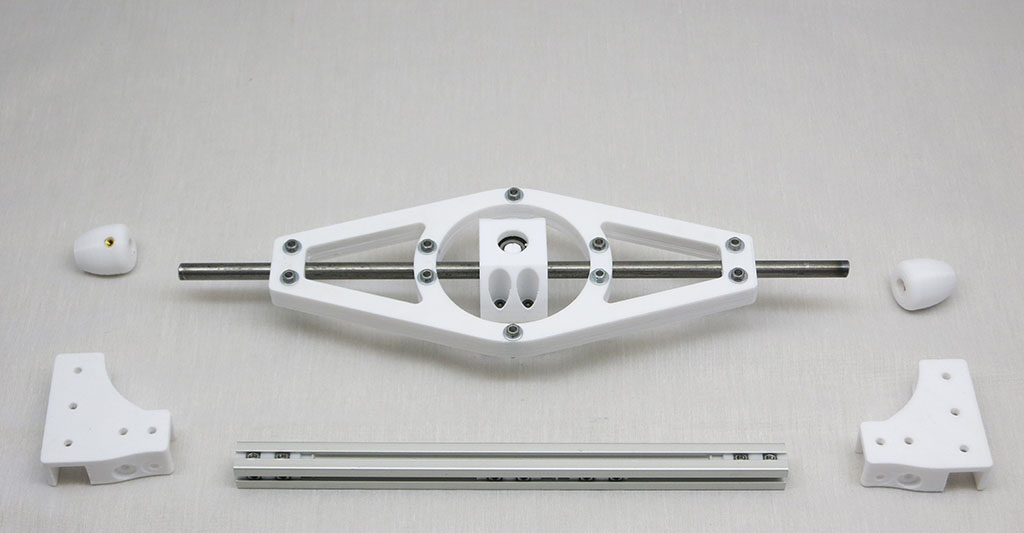
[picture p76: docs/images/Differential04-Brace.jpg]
Brace installed


Insert 2 M3 nut installation tools in center of differential beam side slots for future attachment of differential.

6 M3 nut installation tools, 12 M3x8mm bolts with washers.

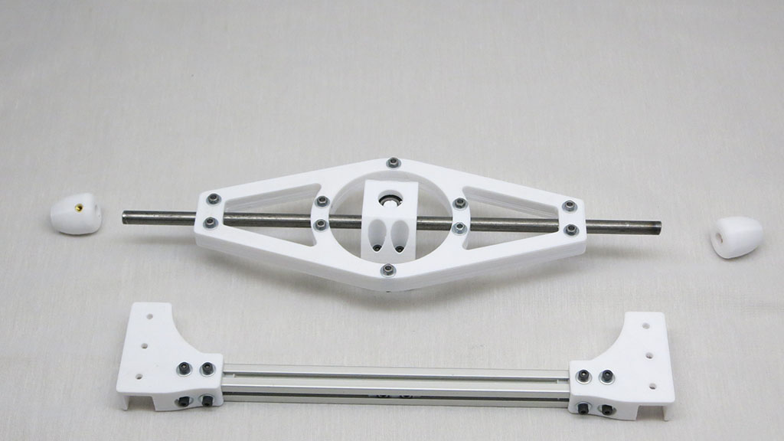
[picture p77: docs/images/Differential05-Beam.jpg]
Left and right brackets for differential beam installed


2 M3 set screws to hold the links in place on the pivot shaft.

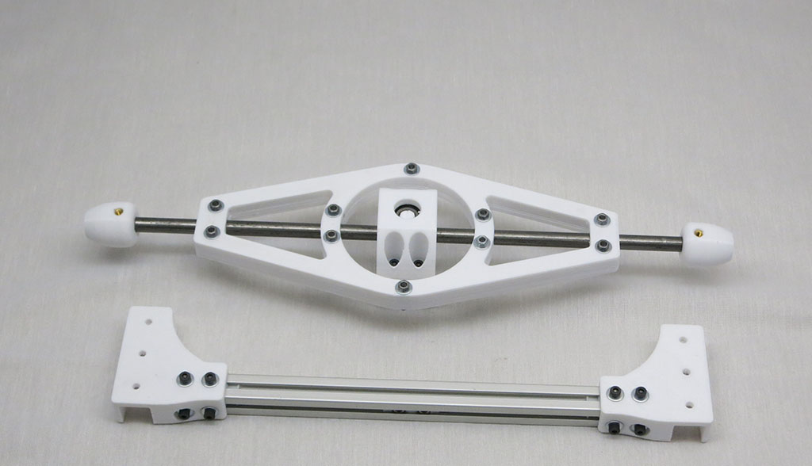
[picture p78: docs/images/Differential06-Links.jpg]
Links at end of pivot bar installed


Bolt the differential onto the beam with 4 M3x8mm bolts with washers and the 2 previously installed M3 nut installation tools.

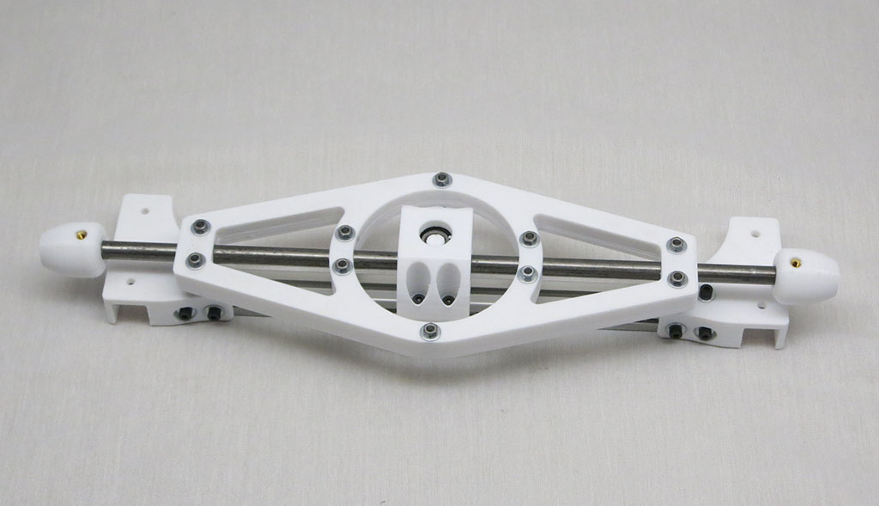
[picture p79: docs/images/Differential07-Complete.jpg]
Differential complete


Bolt differential onto body box with 12 M3x8mm bolts with washers.

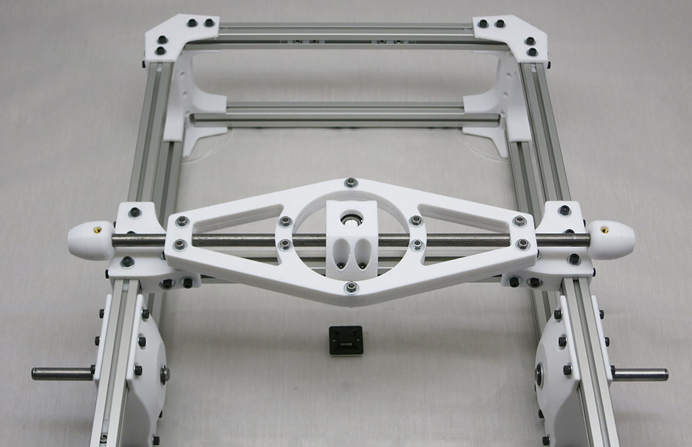
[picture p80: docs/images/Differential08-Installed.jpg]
Differential mounted on body


The Differential Ends should be about 20mm from the Rocker Body mounts. The distance will vary slightly, depending on the length of the turnbuckle used.

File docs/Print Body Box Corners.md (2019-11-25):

# Body Box Corners

These pieces make up the four corners of Sawppy's main equipment bay. They are connected to each other
via aluminum extrusion beams. Each corner has four holes for M3 thread heat-set inserts, as preparation
for future sensors installation.

**CAD source** [Body Corner](https://cad.onshape.com/documents/43678ef564a43281c83e1aef/w/392bbf8745395bc24367a35c/e/96f29082d5f6df96d18015bb)

**3D Printing STL File:** [Body Corner.stl](../STL/Body%20Corner.stl)

**3D Printing Notes**
* We will need 4 of these, one for each corner of rover equipment bay.
* Lay the shape on print bed as shown in picture below for best strength from print layer orientation.
* Example print durations:
  * Fast PLA rough draft: 4 hours each * 4 units = 16 hours total.
  * Slow PETG final draft: 6.5 hours each * 4 units = 26 hours total.

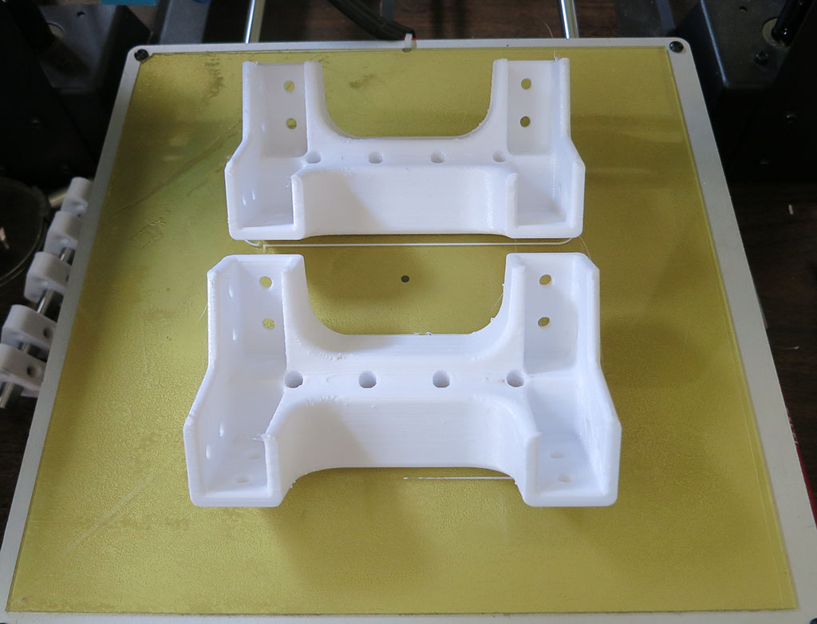
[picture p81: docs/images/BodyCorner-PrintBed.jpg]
Box corner on print bed


**Post-Processing:**

No special processing required.

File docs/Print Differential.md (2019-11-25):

# Differential

The differential on Sawppy is different from the differential in an automotive drivetrain. Instead of
distributing different forces across different drive wheels, this differential distributes suspension
forces across the two sides. It is a key part of how the [rocker-bogie suspension](https://en.wikipedia.org/wiki/Rocker-bogie)
keeps all six wheels on the ground.

**CAD source** [Differential](https://cad.onshape.com/documents/43678ef564a43281c83e1aef/w/392bbf8745395bc24367a35c/e/ded3b96eec03ac1553f6b0a8)
with brackets to mount to body in [Body Box Mounts](https://cad.onshape.com/documents/43678ef564a43281c83e1aef/w/392bbf8745395bc24367a35c/e/4b42dffa042b70b94b3d0d85)

**3D Printing STL Files:**
* [DiffBrace.stl](../STL/DiffBrace.stl) * 2
* [DiffEnd.stl](../STL/DiffEnd.stl) * 2 (Mirror one of them)
* [DiffLink.stl](../STL/DiffLink.stl) * 2
* [DiffLower.stl](../STL/DiffLower.stl) * 1
* [DiffUpper.stl](../STL/DiffUpper.stl) * 1
* [Rod Support.stl](../STL/Rod%20Support.stl) * 2

**3D Printing Notes:**
* The [differential brace](../STL/DiffBrace.stl) is a large part that needs to be rotated 45 degrees
in order to fit on a 200mm x 200mm print bed.
* Aside from the differential brace, everything else can be printed together.

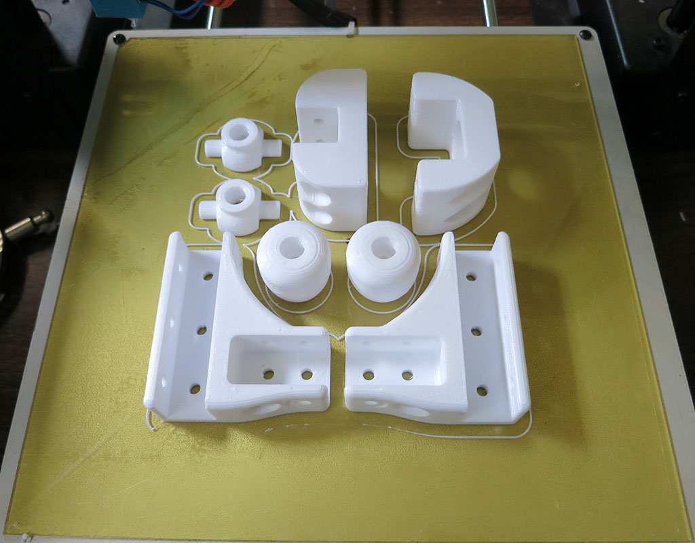
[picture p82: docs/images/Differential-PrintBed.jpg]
Differential Parts


**Post-Processing:**

The most dimension-critical part is the differential link. It needs to grab onto the 8mm shaft used as differential
rod via set screws. It also needs M3 threads to connect (via a turnbuckle) to the suspension rocker arm.

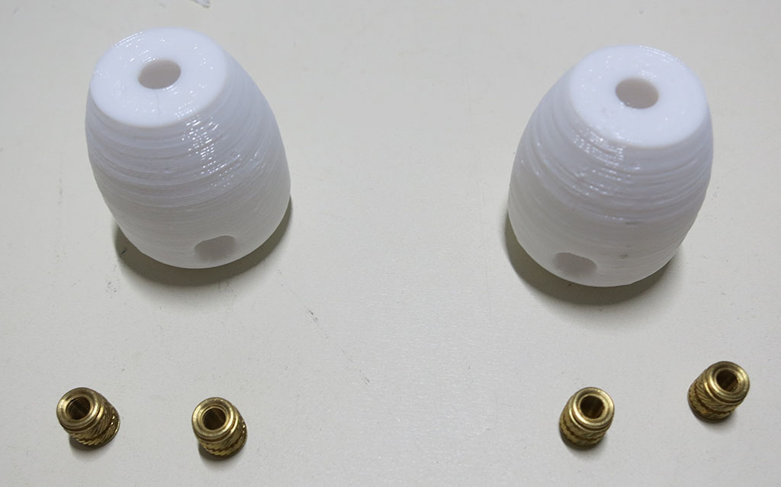
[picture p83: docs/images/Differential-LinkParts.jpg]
Differential link parts


Use 8mm reamer to ensure good fit on 8mm rod used for differential rod.

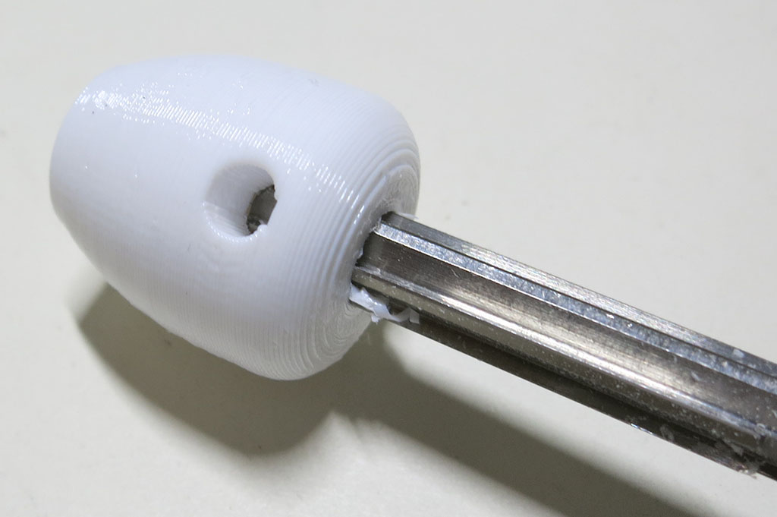
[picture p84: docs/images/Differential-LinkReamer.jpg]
Differential link 8mm cleanup


The pair of rod supports also need 8mm reamer cleanup.

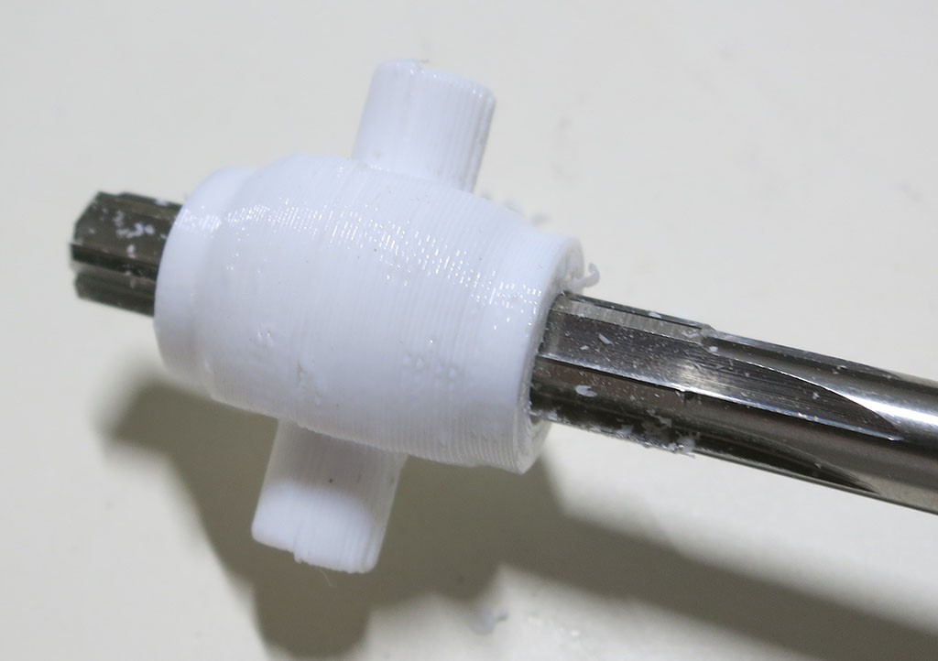
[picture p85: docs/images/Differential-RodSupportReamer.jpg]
Differential rod support 8mm cleanup


The lower differential part needs four M3 thread heat set inserts. The upper and lower parts also each get a bearing.

Differential upper and lower with bearings and M3 inserts

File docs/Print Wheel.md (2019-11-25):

# Wheel

The rover wheel is the most intricate, time-consuming part to print.
It will likely require a few tries while tuning 3D slicer for optimal output.

**CAD source** [Wheel Parts](https://cad.onshape.com/documents/43678ef564a43281c83e1aef/w/392bbf8745395bc24367a35c/e/97ee620b9a27889d24f20c4d)

**3D Printing STL File:** [Wheel.stl](../STL/Wheel.stl)

**3D Printing Notes:**
* The wheel is designed to print without supports, outer face of the wheel against the bed.
* The wheel spoke and perimeter is an even multiple of nozzle diameter and should print in a few large continuous motions.
But the thin dimensions could confuse some slicers. If it generates paths broken up into an excessive number of segments, adjust your slicer settings.
* The rover will need 6 wheels. Printing half of them in a left/right mirror-image is an optional aesthetic choice.
Note that the [real Curiosity rover](https://www.jpl.nasa.gov/video/details.php?id=910) does not left/right mirror its wheel spoke design.
* Example print durations:
  * Fast PLA rough draft: 7.5 hours per wheel * 6 wheels = 45 hours total
  * Slow PETG final draft: 12 hours per wheel * 6 wheels = 72 hours total

Wheel on 3D printer bed

**Post-Processing**

Estimated Time: 2 minutes per wheel * 6 wheels = 12 minutes total.

**Tools:**
* 8mm reamer with drill
* 4mm or 5/32" drill bit, slightly smaller is OK as precision does not matter.

**Parts**
* 3D printed rover wheel

There is a thin layer of filament to help our printer bridge the bolt hole during printing. Now that printing is complete,
they are no longer necessary and should be removed with the 4mm (or smaller) drill bit. In this image, one hole has been
cleaned up, one is in progress, and one awaits cleanup.

Wheel bridge removal

We want our 8mm steel drive shaft to fit snugly within the wheel's center. To help with this, use an 8mm reamer
to bring the center hole into precise dimension.

Wheel axle hold precisely reamed to 8mm

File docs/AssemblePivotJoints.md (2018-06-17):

# Pivot Joints Assembly

This page covers assembly of all the steering/pivoting elements of rover suspension.

**Estimated Time:** 10 minutes total.

## Corner Steering

**Parts:**
* 4 * [Corner steering components](Print%20Corner%20Steering%20Joints.md)
* 4 * [Steering shafts](Shaft8mm.md)
* 8 * Retaining E-clips

Corner module parts

For each corner steering module, use 2 e-clips to hold a steering shaft in place.

Corner modules complete

## Bogie Joint

**Parts:**
* 2 * [Bogie Joint](Print%20Suspension%20Bogie%20Joints.md)
* 2 * [Bogie Pivot Shaft](Shaft8mm.md)
* 6 * Retaining E-clips

Bogie joint parts

Use 3 e-clips to install shaft into the joint, and both elements of the joint onto the shaft.

Bogie joint complete

After all parts have been verified to fit, separate them again. They will be built into
different sub-assemblies before meeting back up again later.

Bogie joint separated

Repeat for mirror-image bogie joint for other side of rover.

## Rocker Joint

**Parts:**
* 2 * [Rocker Joint](Print%20Suspension%20Rocker%20Joints.md)
* 2 * [Rocker Pivot Shaft](Shaft8mm.md)
* 6 * Retaining E-clips

Rocker joint parts

Use 3 e-clips to install shaft into the joint, and both elements of the joint onto the shaft.

Rocker joint complete

After all parts have been verified to fit, separate them again. They will be built into
different sub-assemblies before meeting back up again later.

Rocker joint separated

Repeat for other side of rover.

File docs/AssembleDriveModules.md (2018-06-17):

# Drive Module Assembly

This step builds drive modules for all six wheels. Four of these modules are for steerable corners
and the remaining two are the non-steering middle wheels.

**Estimated Time**: 6 minutes each * 6 units = 36 minutes total.

## Steerable Drive Module

**Parts:**
* 1 * [Servo actuator module](AssembleActuatorModule.md)
* 1 * [Steering knuckle](Print%20Steering%20Knuckle.md)
* 1 * [8mm wheel axle/drive shaft](Shaft8mm.md)
* 1 * [Wheel hub](Print%20Wheel%20Hub.md)
* 2 * Retaining E-clips
* 2 * M3 set screws
* 2 * M3x8mm bolts
* 2 * M3 washers

Steerable Drive Module Parts

Use the two E-clips to install 8mm drive shaft into steering knuckle.

Drive shaft installed

Use the two M3x8mm bolts, along with their washers, to install the servo actuator module.
Slide wheel hub onto drive shaft.

Servo and hub installed

The M3 thread heat-set insert in the hub should be facing inward, away from the wheel.
(And this camera's viewpoint.)
This way when the wheel mounting bolts are tightened, the force will pull the heat set
insert tighter into the hub. If hub is installed reversed, wheel bolt force will be trying
to pull the heat set insert out of the hub which is undesirable.

Hub installation direction makes heat set insert face away

Install set screws into servo coupler and wheel hub to attach them to the drive shaft.
Use thread-locking compound (Loctite Blue 242 shown) to keep the set screws in place.

Steerable module complete

Repeat for a total of four steerable drive modules.

## Non-Steerable Drive Module

Similar to above, except all the same parts are bolted onto the [non-steering fixed knuckle](Print%20Fixed%20Knuckle.md).

Non-steerable Drive Module Parts

Repeat and assemble mirror-image module for the other side of the rover.

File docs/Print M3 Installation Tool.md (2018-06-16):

# M3 Nut Installation Tool

These small tools help hold M3 nuts at the correct spacing for rover assembly. Each is single
use as they are left in place after rover assembly.

**CAD source** [Clips and Shims](https://cad.onshape.com/documents/43678ef564a43281c83e1aef/w/392bbf8745395bc24367a35c/e/885c41055d6e58059a790a21)

**3D Printing STL Files:**
* [Clip2n125.stl](../STL/Clip2n125.stl) for holding two M3 nuts 12.5mm apart.
* [Clip3n20.stl](../STL/Clip3n20.stl) for holding three M3 nuts 20mm apart.

**3D Printing Notes**
* These tools are single nozzle width wide, so individually they are very fast to print in a single motion.
* Since they are fast and take very little material, go ahead and print extras. Some will be unusable
due to random 3D printer problems, some may break in use, and some will be lost because they're so small.
* We will need at least 12 copies of Clip3n20.stl
* We will need at least 88 copies of Clip2n125.stl

M3 nut installation tools on printer bed

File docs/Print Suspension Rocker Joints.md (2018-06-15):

# Suspension Rocker Joints

These parts make up the main suspension pivot point against the main chassis box.

### Rocker

This part houses the two bearings for the rocker assembly to pivot on, and connects to two aluminum extrusion beams.
One leading to the bogie pivot joint, the other leading to a front corner. The top of this part connects to the
suspension differential.

**CAD source** [Rocker](https://cad.onshape.com/documents/43678ef564a43281c83e1aef/w/392bbf8745395bc24367a35c/e/4a687fb6a85c60c7ec293eb2)

**3D Printing STL File:** [Rocker.stl](../STL/Rocker.stl)

**3D Printing Notes**
* We will need 2 of these, mirror-image of each other. One for each side.
* Example print durations:
  * Fast PLA rough draft: 3 hours each * 2 sides = 6 hours total.
  * Slow PETG final draft: 5.5 hours each * 2 sides = 11 hours total.

**Post-Processing:**

Estimated time: 3 minutes each * 2 units = 6 minutes total.

**Parts:**
* 2 * 3D printed pieces, one mirror of the other.
* 4 * bearings
* 2 * M3 thread heat set inserts

Rocker parts

Remove thin bridge assist layers from four bolt holes facing the print bed.

Install M3 thread heat-set insert for future connection to differential.

Rocker heat set insert

Install bearings.

Rocker complete

### Rocker body mount

This part connects the rocker-bogie suspension of one side to the main chassis equipment box. It holds
the 8mm shaft for the suspension to pivot upon, and bolts to the two lengthwise body extrusion beams.

**CAD source** [Box body mounts](https://cad.onshape.com/documents/43678ef564a43281c83e1aef/w/392bbf8745395bc24367a35c/e/4b42dffa042b70b94b3d0d85)

**3D Printing STL File:** [Rocker Body Mount.stl](../STL/Rocker%20Body%20Mount.stl)

**3D Printing Notes**
* We will need 2 of these. This part is symmetric so no need for mirroring.
* Example print durations:
  * Fast PLA rough draft: 3.5 hours each * 2 sides = 7 hours total.
  * Slow PETG final draft: 8 hours each * 2 sides = 16 hours total.

**Post-Processing:**

Estimated time: 1 minutes each * 2 units = 2 minutes total.

Use 8mm reamer to clean up hole for suspension pivot shaft.

Rocker body mount reamer cleanup

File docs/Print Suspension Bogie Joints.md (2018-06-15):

# Suspension Bogie Joint

These two parts build a pivot joint for the bogie portion of Sawppy's [Rocker-Bogie suspension](https://en.wikipedia.org/wiki/Rocker-bogie).

**CAD source** [Bogie Joint](https://cad.onshape.com/documents/43678ef564a43281c83e1aef/w/392bbf8745395bc24367a35c/e/bc12cd957a8285083c1ffbad)

### Bogie Pivot

This part houses the two type 608 bearings and two aluminum extrusion beams, one connecting to mid wheel assembly
and the other connecting to rear corner wheel assembly.

**3D Printing STL File:** [Bogie-Wheels.stl](../STL/Bogie-Wheels.stl)

**3D Printing Notes**
* We will need 2 of these, mirror-image of each other. One for each side.
* Example print durations:
  * Fast PLA rough draft: 2 hours each * 2 sides = 4 hours total.
  * Slow PETG final draft: 4 hours each * 2 sides = 8 hours total.

**Post-Processing:**

Estimated time: 2 minutes per corner * 2 sides = 4 minutes total.

**Parts:**
* 2 * 3D printed bogie pivot
* 4 * 608 type bearings

Parts for bogie pivot

Use a drill to remove bridge assist layers on 4 bolt holes facing the print bed.

Remove bridge assist from bogie pivot

Install two bearings - one left and one right - onto each pivot piece.

### Bogie Fixed

This will become part of the rocker assembly, housing the 8mm shaft the bogie will pivot on.

**3D Printing STL File:** [Bogie-Body.stl](../STL/Bogie-Body.stl)

**3D Printing Notes**
* We will need 2 of these, mirror-image of each other. One for each side.
* Example print durations:
  * Fast PLA rough draft: 1 hours each * 2 sides = 2 hours total.
  * Slow PETG final draft: 1.5 hours each * 2 sides = 3 hours total.

**Post-Processing:**

Estimated time: 2 minutes per corner * 2 sides = 4 minutes total.

Use a reamer to clean up the 8mm hole for bogie pivot shaft.

Clean up 8mm hole

Use a drill to remove bridge assist layers on 2 bolt holes facing the print bed.

Remove bridge assist

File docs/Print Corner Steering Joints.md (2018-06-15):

# Corner Steering Joints

These parts, one per corner, hold the steering actuators along with the steering shaft.
Plus auxiliary support mechanisms like the 608 bearings supporting the steering shaft.
Each of these sit on top of a steering knuckle and associated steerable wheel assembly.

### Front corners

**CAD source** [Front Corner](https://cad.onshape.com/documents/43678ef564a43281c83e1aef/w/392bbf8745395bc24367a35c/e/9ae94dbd0d5c2040aede037a)

**3D Printing STL File:** [Front Corner.stl](../STL/Front%20Corner.stl)

**3D Printing Notes**
* We will need 2 of these, mirror-image of each other. One for each front corner.
* Example print durations:
  * Fast PLA rough draft: 4.5 hours each * 2 corners = 9 hours total.
  * Slow PETG final draft: 5.2 hours each * 2 corners = 10.4 hours total.
  
**Post-Processing:**

Estimated time: 2 minutes per corner * 2 corner = 4 minutes total.

**Parts:**
* 2 * 3D printed front corner pieces, one mirror of the other.
* 4 * 608 type bearings

Front corner parts

Use a drill to remove bridge assist layers on 4 bolt holes facing the print bed.

Install two bearings - one top and one bottom - onto each front corner piece.

Front corner complete

### Rear corners

**CAD source** [Rear Corner](https://cad.onshape.com/documents/43678ef564a43281c83e1aef/w/392bbf8745395bc24367a35c/e/223fadf8466f52bf16bdc5f7)

**3D Printing STL File:** [Rear Corner.stl](../STL/Rear%20Corner.stl)

**3D Printing Notes**
* We will need 2 of these, mirror-image of each other. One for each rear corner.
* Example print durations:
  * Fast PLA rough draft: 4 hours each * 2 corners = 8 hours total.
  * Slow PETG final draft: 4.7 hours each * 2 corners = 9.4 hours total.

**Post-Processing:**

Estimated time: 2 minutes per corner * 2 corner = 4 minutes total.

**Parts:**
* 2 * 3D printed rear corner pieces, one mirror of the other.
* 4 * 608 type bearings

Use a drill to remove bridge assist layers on 4 bolt holes facing the print bed.

Install two bearings - one top and one bottom - onto each rear corner piece.

Rear corner complete

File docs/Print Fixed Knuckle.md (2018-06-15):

# Fixed Knuckle

The two fixed knuckles connect the middle non-steerable wheels to the aluminum extrusion beams making up the suspension structure.

**CAD source** [Wheel Parts](https://cad.onshape.com/documents/43678ef564a43281c83e1aef/w/392bbf8745395bc24367a35c/e/97ee620b9a27889d24f20c4d)

**3D Printing STL File:** [Fixed Knuckle.stl](../STL/Fixed%20Knuckle.stl)

**3D Printing Notes:**
* We will need two of these objects, one for each side of rover suspension. One must be printed mirror-image of the other.
* Example print durations:
  * Fast PLA rough draft: 3.5 hours each * 2 knuckles = 7 hours total.
  * Slow PETG final draft: 5.5 hours each * 2 knuckles = 11 hours total.

**Post-Processing**

Estimated time: 2.5 minutes per knuckle * 2 knuckles = 5 minutes total.

**Tools:**
* (Optional) C-clamp or arbor press

**Parts:**
* 3D printed fixed knuckle
* 2 * Type 608 bearings

Fixed Knuckle Parts

Bearings are installed in the same way they were installed for the [steering knuckle](Print%20Steering%20Knuckle.md).

Fixed Knuckle with bearings installed

Repeat for mirror-image knuckle for other side of rover.

Mirrored Fixed Knuckle Complete

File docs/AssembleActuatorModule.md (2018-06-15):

# Servo Actuator Module Assembly

These instructions prepare a serial bus servo for integration into an actuator module for Sawppy the Rover.

**Estimated Time**: 6 minutes per module * 10 modules = 1 hour total.

## Servo preparation

10 serial bus servos are used to control Sawppy the Rover - 4 for steering each of the corner wheels,
and 6 to drive each of the wheels. A few preparatory steps should be taken before integration with printed parts.

These servos are assigned to a default address from the factory. They need to be assigned unique
addresses that do not conflict with any other servo on the same serial bus. Consult the manual
for details. After an address is assigned, label the servo with its address for later identification.
The servo address reassignment tool should also allow you to do a quick test to verify that the
servo works properly. After you test servo motion, be sure to reset back to center position before
disconnecting power. This will be important when setting up the steering servos in the next step.

Servo ID

## Install shaft coupler

**Parts:**
* Serial bus servo
* [Servo shaft coupler](Print%20Servo%20Parts.md)
* 4 * installation screws. The serial bus servo comes with some installation screws, but they have proven
to be too short for long-term durability. The fastener used in the pictures below are [McMaster-Carr #98685A220](https://www.mcmaster.com/#98685a220)
1/4" long Philips #2 brass screw.

Servo coupler parts

Verify that the 3D-printed coupler is free of printer debris and is of proper dimensions by installing
the screws and verify they can extend far enough for the threads to properly engage the servo horn.

Coupler screw length verification

Once verified, install the coupler onto the servo horn. For the four steering servos, they need to be
at (or at least close) to their center position. The coupler should then be installed so two of them have
the set screw facing one side and two of them have set screw pointing to the other side.

Servo set screw orientation

For the six driving servos, coupler set screw orientation does not matter.

Slide the bracket over the servo to complete a servo actuator module for Sawppy the Rover.

Actuator module complete

Repeat procedure for a total of ten modules.

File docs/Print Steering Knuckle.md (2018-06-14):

# Steering Knuckle

The steering knuckle connects the steering shaft to the driving shaft. Its convoluted shape 
was dictated by its [design constraints](https://newscrewdriver.com/2018/05/16/sawppy-the-rovers-steering-knuckle/) 
and it is a key part of rover suspension geometry.

**CAD source** [Wheel Parts](https://cad.onshape.com/documents/43678ef564a43281c83e1aef/w/392bbf8745395bc24367a35c/e/97ee620b9a27889d24f20c4d)

**3D Printing STL File:** [Steering Knuckle.stl](../STL/Steering%20Knuckle.stl)

**3D Printing Notes:**
* This object has all the dimension-critical feature types found in this project, 
it may require several prints to tune your 3D printing settings.
  * M3 thread heat-set inserts.
  * 8mm hole for steering shaft.
  * 22mm hole for 608 type bearing.
* We will need four of these objects, one for each corner. Mirroring two them is an optional aesthetic choice.
* Example print durations:
  * Fast PLA rough draft: 4.25 hours each * 4 knuckles = 17 hours total.
  * Slow PETG final draft: 8.75 hours each * 4 knuckles = 35 hours total.

The 22mm hole for 608 type bearing is large and it is likely your printer couldn't print a clean top edge.
This is OK and might even be an advantage! If your hole is slightly too large, these little pieces of 
dangling filament can help wedge the bearing in place.

Steering knuckle imperfect bearing hole

**Post-Processing**

Estimated time: 9 minutes per knuckle * 4 knuckles = 36 minutes total.

**Tools:**
* Drill with 8mm reamer
* Soldering iron
* M3 bolt with washer and hex wrench.
* (optional) C-clamp

**Parts:**
* 3D printed steering knuckle
* M3 thread heat set insert
* 2 * Type 608 bearings

Steering knuckle parts

Clean up the 8mm hole for the steering shaft with 8mm reamer.

Steering knuckle reamer

Install M3 thread heat-set insert.

Steering knuckle set screw insert

Install bearings in their holes, one inside and one outside. Ideally they should be a snug finger-press fit. 

Steering knuckle inside bearing
Steering knuckle outside bearing

If the holes are slightly too large, the bearings might fall out until drive shaft is installed with
retaining clips. If the holes are far too large the rover's wheel direction would be unpredictable
causing erratic travel motion. It may be best to adjust your settings and print a new knuckle.

If the holes are slightly too small, use a C-clamp or similar tool to help install the bearings.
(The best tool is an arbor press, if you have access to one.) If the hole is far too small, you
can try carving out the excess plastic but it is hard to keep the bearings centered that way. It
may be best to adjust your settings and print a new knuckle.

Steering knuckle bearing installed with clamp

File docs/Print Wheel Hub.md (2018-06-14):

# Wheel Hub

The wheels bolt onto this hub, which has a set screw to grab on to the 8mm drive shaft
transferring power from the servo drive actuator module.

**CAD source** [Wheel Parts](https://cad.onshape.com/documents/43678ef564a43281c83e1aef/w/392bbf8745395bc24367a35c/e/97ee620b9a27889d24f20c4d)

**3D Printing STL File:** [Wheel Hub.stl](../STL/Wheel%20Hub.stl)

**3D Printing Notes**
* The set screw hole is identical to that on the servo coupler and shares the same issues. 
See servo coupler instructions for more details.
* We will need 6 of these, one for each wheel. Also: consider having one or two extra on hand as spare parts.
* Example print durations:
  * Fast PLA rough draft: 14 minutes each * 6 hubs = 1.5 hours total.
  * Slow PETG final draft: 30 minutes each * 6 hubs = 3 hours total.
  
**Post-processing**

Estimated time: 10 minutes per hub * 6 hubs = one hour total.

**Tools:**
* Drill
* 8mm reamer
* Soldering iron
* 10 to 14mm long M3 bolt, with washer and hex wrench.

**Parts:**
* 3D printed wheel hub
* 4 * M3 heat-set insert

Parts list

Use 8mm reamer to clean up the center hole for the drive shaft.

The M3 thread heat-set insert for the set screw going in to the side is installed the same way 
as the identical part in servo coupler. See servo coupler instruction for details.

Set screw insert

The remaining 3 heat set inserts are for us to bolt the wheels onto. Since they are easy to 
install we do not need the extra M3 bolt tool. We do, however, still have to be careful about 
maintaining alignment. In this picture, the heat-set insert is starting to lean off-center and n
eeds to be corrected before it cools and sets at an angle.

Wheel bolt insert

Depending on exact dimensions of heat-set insert and 3D printer settings, the hole may be too small or too large.

If the hole is too large, the inserts will not be able to hold itself in place. try using epoxy 
or other adhesive to glue the insert in place, or try printing hubs with smaller hole dimensions.

If the hole is too small, it will push too much plastic while it melts. "Too much" is when the
bolt hole is no longer accessible from the other side, which is the direction we'll be bolting
the wheel from. In this picture, the hole on the right was too small and there's excess plastic
that needs to be removed. (Try an X-Acto blade.) To resolve a slightly too-small hole, use a 
drill bit to remove some material before installing the heat set insert. This was done for the
hole on the left, which shows the desired lip of plastic being pushed ahead of it (which will
help keep it in place) without too much excess that blocks bolt access.

Too much plastic

A successfully completed wheel hub will have the heat-set inserts level and flush to one side 
(shown here) and all M3 threads accessible from the reverse side. (not shown)

Wheel hub complete

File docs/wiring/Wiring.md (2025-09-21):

# Wiring

The wiring harness connects each of the motors to the BusLinker board on the
body panel with a cable.

## Terminology
Some notes on termininology (with acknowledgement to
[this NASA JPL Open Source Rover wiring documentation](https://github.com/nasa-jpl/open-source-rover/tree/master/electrical/wiring):
* *Wiring harness* (also called cable harness or wire assembly): the collective term for all the wiring and cables that are run through a system to connect power sources, sensors, data lines, etc. In the case of the rover, this means the cables that feed power to the motors, the control signals to the servos, and the encoder data back to the control boards.
* *Cable*: A group of wires/conductors, usually with an outer sheath.
* *Wire*: A single conductor, solid or stranded core, of any gauge.

## Cables

There are many ways to construct your cables:
1) you can cut the small wires that come with your servos, and splice the cables to the middle.
2) you can purchase connectors that match your servos, as shown below.

Each end of each wire contains a connector to your servo motor:
* For the LX-16A, the Molex mini SPOX connector should be used.
    * [Mini-SPOX 5264 3 Position Housing](https://www.newark.com/molex/50-37-5033/connector-rcpt-3pos-1row-2-5mm/dp/57H1785)
    * [Mini-SPOX 5264 Socket](https://www.newark.com/molex/08-70-1040/contact-socket-22awg-crimp/dp/54H5573)
    * Each servo has two connectors, so you have to daisy chain them.
    * Here is an image of the connector:
      Mini-SPOX 3 Position Connector
* For the LX-224, you can use the JST-2.0-3P connector as shown below.
    * Each servo has three connectors, enabling chaining in serial and/or parallel.

## Harness
There are also several ways to construct your harness.  The bus servos have two or three connectors on them, which are electrically connected together pin-for-pin.  That is, they are electrically parallel.  Thus, you don't really need to worry about if your servos are connected in parallel or daisy-chained, so long as you connect them all pin-to-pin to the BusLinker board.

However you make your harness, it is recommended to enclose them in some sort of sleeve.  You can use the braided sleeves as described at (https://newscrewdriver.com/2018/06/14/expandable-braided-sleeves-neaten-sawppy-the-rovers-wiring/), or spiral wrap similar to (https://www.newark.com/abb-thomas-betts/srpe-250-9-c/spiral-wrap-pe-natural-0-25in/dp/61H6991), or even just judicious use of zip-ties.  But that's what bundles wires into a cable, and cables into a harness, which is much nicer to work with than a birds-nest of individual wires!

1) Knowing this, you can construct your harness to mimic the kinematic structure of the rover - put a Y connection at the rocker joint, another at the bogie joint, etc, then splice your extensions between these connectors.  This is what was done for the original sawppy.

2) You can also use the multiple connectors on the servos to simplify your harness.  That is what is documented below.

Wiring Overview
Wiring diagram for one side of the rover, for the LX-224 configuration.  The other side is identical, except for the cable going to the BusLinker board.  For the LX-16A, you'd need to connect your servos in series or make a break-out board.

Harness diagrams further below were generated with [WireViz](https://github.com/wireviz/WireViz/) and can be re-generated with the *generateHarness.bat/.sh* scripts.
Harness Details

In summary, for the LX-224 configuraiton, you need
* 1x: 82 cm cable from BusLinker to right front wheel
* 1x: 50 cm cable from BusLinker to left front wheel
* 2x: 64 cm cable from front steering servo to rear steering servo
* 2x: 36 cm cable from rear steering servo to middle drive servo
* 4x: 21 cm cables from drive servo to steering servo

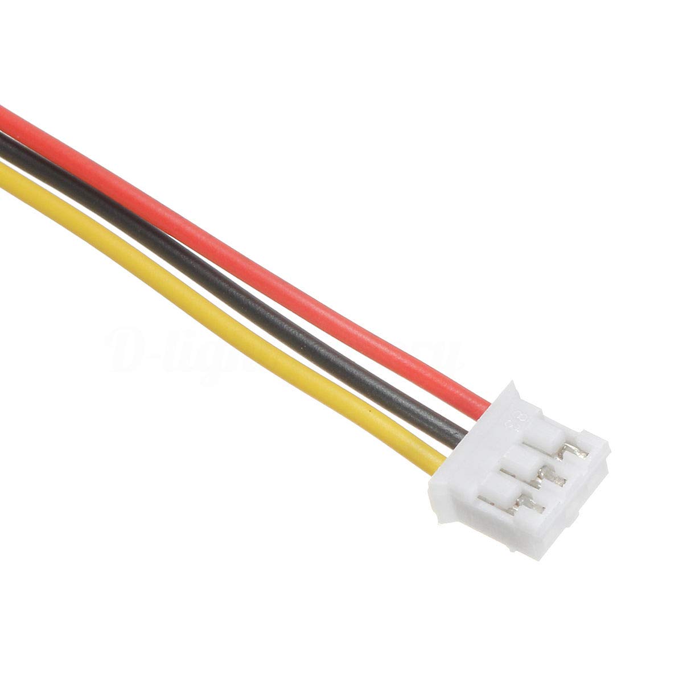
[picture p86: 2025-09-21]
docs/wiring/connector_images/jst-2.0-3p.jpg

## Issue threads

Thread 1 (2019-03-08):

Enhancement - LEXAN BODY SHELL

johndpope, 2019-03-08:
There are dae collada files here that maybe suitable - may need some reworking.
https://bitbucket.org/theconstructcore/curiosity_mars_rover/commits/all

johndpope, 2019-03-08:
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

johndpope, 2019-03-08:
https://www.ebay.com.au/itm/1-10-RC-Car-Lexan-Clear-Body-Shell-200mm-Lexus-LFA-Will-Fit-Yokomo-TAMIYA-HPI-/121875609990

was imaging a cover like this -
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

johndpope, 2019-03-08:
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

https://www.youtube.com/watch?v=CQc6gAWl4dY

johndpope, 2019-03-08:
https://www.youtube.com/watch?v=QuOAk0pgsGY

johndpope, 2019-03-10:
https://www.lego.com/en-us/service/buildinginstructions/search?initialsearch=42081#?text=42081
came across this volvo concept - looks mint

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

johndpope, 2019-03-10:
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
![Uploading Screen Shot 2019-03-10 at 9.36.48 AM.png…]()
![Uploading Screen Shot 2019-03-10 at 9.36.39 AM.png…]()

Roger-random, 2019-03-10:
A Lexan shell would be a good optional component for Sawppy builders who want to make their rovers resemble Curiosity not just in mechanical geometry but also in cosmetic appearance. At the moment my focus is not on the rover's looks, but if anyone else wants to make these cosmetic shells happen that would be fantastic!

Playville, 2019-03-10:
Hi Roger!
I just finished the mechanical build a few minutes ago and started planning on some “cosmetics”, especially on the body. As soon as I’m done id love to share the inventor-Files if you like to?

johndpope, 2019-03-11:
Hi @playville - there are some png images inside the official 3D project (first link at top) that I guess could be used as decals.

Feel free to post screen shots of work in progress. Would love to see. When your happy you can submit a pull request to merge your updates into project. Welcome  to the world of open source.

johndpope, 2019-03-11:
https://bitbucket.org/theconstructcore/curiosity_mars_rover/src/94974385f14a1f229bf436f91552ab6384fd89b4/curiosity_mars_rover_description/meshes/tex_01.png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

johndpope, 2019-03-16:
Found this -

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

https://www.thingiverse.com/thing:3493597

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

https://www.thingiverse.com/thing:1606181

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

Roger-random, 2019-07-21:
I'm happy to share that one of the Sawppy builders has made great progress at building cosmetic add-ons to make Sawppy look like Curiosity Rover. Please see [Laura McKeegan's project CJ ("Curiosity, Jr.") rover on hackaday.io](https://hackaday.io/project/165094).

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

And for anyone else who wishes to undertake a similar project, I've shared all the [3D resources I've found for Curiosity rover](https://newscrewdriver.com/2019/06/25/curiosity-rover-3d-resources/). The best one seems to be the Blender model released by NASA JPL.

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

johndpope, 2023-09-01:
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
![00003-630438868](https://github.com/Roger-random/Sawppy_Rover/assets/289994/6209cf4c-4f4c-4541-ad8
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
6-9f1c03370418)
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

hi @Roger-random  - you might be interested to play around with stable diffusion
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

Here I just prompt
 "mars curiosity rover lexan body shell, technical drawing, pencil![Uploading 00
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
011-2492057212.png…]()

also not sure you saw this -
https://www.youtube.com/watch?v=fY32WFY-LuM&ab_channel=RobotGarden

Closed 2019-07-21.

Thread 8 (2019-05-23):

onShape CAD document

digitalsmeg, 2019-05-23:
Is this intended to be behind a paywall?  I know models can be shared publicly but the Swappy document is forcing me to register with onShape just to view it. Unless I overlooked it, do you guys have a CAD file of the entire build somewhere in this repo?

Roger-random, 2019-05-23:
There is no paywall but you do have to register with Onshape on their free tier for makers and hobbyists. https://www.onshape.com/products/free

digitalsmeg, 2019-05-23:
I totally missed that. Thanks for the link!

Closed 2019-05-23.

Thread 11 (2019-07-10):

Things to maybe add to Parts List

adamgreen, 2019-07-10:
As I was reading through the documentation to put together a list of the things I have to order, I ended up adding a few things to my list that didn't show up in docs/Parts List.md

Maybe there should be a tools section to give a list of tools that someone who is newer to these type of builds (such as myself) might not already have in their possession?
* 8mm Reamer
* Metric Tap & Die Set (A M3 tap specifically)

In the hardware section, I don't see mention of any **M3x16mm socket head screws** but I do see 10 of them being mentioned in the differential assembly instructions. Should these be added to the main hardware list?

What about a list of electronic components required? No matter if a person uses an Arduino or a RaspberryPi, they will need the **LewanSoul BusLinker** hardware to interface with the LX-16A servos which are included in the list.

I just opened this Issue to start a conversation about this topic. I can draft up a PR in the future based on resulting feedback.

As this is my first issue here, I just wanted to thank you for all of the work involved in this project. I really appreciate it! There is an awesome amount of work here!

Roger-random, 2019-07-13:
Thanks for the feedback and opening this discussion! I always appreciate people who go through the instructions and send feedback based on their first hand experience.

Here's my understanding of what you've conveyed:

1. **M3x16mm socket head screws**: yes I agree they missing and should be listed on docs/Parts%20List.md. Related: Not only are they used on the differential, they are also used to install Sawppy wheels to their hub. I didn't create an entire page on wheel installation thinking it was straightforward. But that also meant I had just the line "Once all the wheels are bolted on to the suspension" without mentioning the M3x16mm fastener and associated washers. Oops.

2. **8mm reamer, M3 tap, etc.**: I don't think they belong on the parts list as they're not actually parts of the rover. However, I agree it would make sense to have a page dedicated to discussing tools involved in building a Sawppy. Outline all the goals and different ways to accomplish that goal. Like how the 8mm shafts would ideally be cut on a metalworking lathe, but in the absence of a lathe, they can be cut with a Dremel. As long as the goal is met.

3. **Electronics components**: I didn't place much emphasis on precisely outlining the electronics, because I anticipated people would customize and do their own thing anyway. Do you think it is valuable to have a single "prescribed" set of electronics directions? Side note: it is actually possible to make an Arduino communicate directly with the LX-16A servos in half-duplex, skipping the need for BusLinker, with a software serial port that transmits and receives on the same pin.

adamgreen, 2019-07-14:
@Roger-random Thanks for the response!

1. **M3x16mm socket head screws:** I think your response contains enough information for me to start creating a PR to address it.
2. **8mm reamer, M3 tap, etc.:** I could start a page for required tools: 8mm reamer, M3 tap, 1.5 and 2.5mm Allen key (hex key) wrenches. You make a good point about some of the other items like preparation of the 8mm shafts.
3. **Electronic components:** I agree with your comments on the electronics. I hadn't investigated the LX-16A servos in much detail yet. I was waiting for mine to arrive first. I had suspected that the BusLinker might not be required so I am happy to hear that is the case.

Roger-random, 2019-07-21:
Thanks for your additions to the documentation. (Sorry for the delay - I had missed my notifications.) I'll close this issue to reflect the merged changes.

You said you're waiting for your servos to arrive. Once you've had some hands-on time with them, I'm sure you'll have feedback on how we can improve Sawppy documentation for electronics components.

Please feel free to open new issues when that comes up, I look forward to reading them.

adamgreen, 2019-07-22:
> I'll close this issue to reflect the merged changes.

Cool! I had planned to do the same but you saved me the effort :)

> You said you're waiting for your servos to arrive. Once you've had some hands-on time with them, I'm sure you'll have feedback on how we can improve Sawppy documentation for electronics components.

Actually I was waiting for pretty much all of the bits and pieces for my Sawppy build to arrive. Most of the parts arrived last week (including the servos).
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

I am just waiting on my 3D printer now. Once it arrives, I will start building. I have some software / hardware items that I want to dig into in the meantime. This includes hopefully playing with the servos this week.

adamgreen, 2019-08-23:
> Side note: it is actually possible to make an Arduino communicate directly with the LX-16A servos in half-duplex, skipping the need for BusLinker, with a software serial port that transmits and receives on the same pin.

I recently started playing with the LX-16A serial servos. Pretty cool! I actually ended up needing to use the half duplex method to communicate with the servos anyway as the Cortex-M3 microcontroller I was using couldn't sink enough current to drive that BusLinker board with its strong pull-ups. I took one of mine apart and posted a [few notes about what I found inside](https://github.com/adamgreen/Ferdinand20#lewansoul-lx-16a-servo-teardown).

Roger-random, 2019-08-25:
Thanks for the detailed teardown notes. This will be very useful guide when I take apart my LX-16A that [failed short at Maker Faire.](https://newscrewdriver.com/2019/06/09/sawppy-emergency-field-repair-at-maker-faire-bay-area-2019-steering-servo/)

adamgreen, 2019-08-25:
@Roger-random Are you hoping to repair your failed servo or just root cause it? Either way, good luck! Sounds like a fun debugging project.

Roger-random, 2019-08-26:
I don't expect to put that servo back into active use, I'm mostly curious to see if the cause of the failure could be determined. If it could be repaired and put into some secondary/backup role, it would be nice but not a goal.

I read through more of your Ferdinand20 project documents (beyond the LX-16A teardown) and it sounds like a great project! I worry about Sawppy's speed, though. I modeled after Curiosity which is no speed demon with a top speed of 4cm/sec. Sawppy's top speed is significantly slower than other RoboMagellan entries. And while you can put faster motors inside the wheels, the suspension geometry is also optimized for low speed operation and would not absorb the shocks of high speed impact with obstacles. Hopefully this is something you've taken into consideration.

adamgreen, 2019-08-26:
> I don't expect to put that servo back into active use, I'm mostly curious to see if the cause of the failure could be determined. If it could be repaired and put into some secondary/backup role, it would be nice but not a goal.

I saw [this thread on the Trossen Robotics forum](http://forums.trossenrobotics.com/showthread.php?14684) where a user discusses the analysis of a premature failure in one of their LX-16A servos. They indicated that the brushes on the motor had failed. From my teardown, I thought the servos looked like they were quite well built. However, the originator of that forum thread indicates that the motors are being provided with more than their rated voltage in the servos.

> I worry about Sawppy's speed, though.

I am aware of that issue. At this point, I care more about completing the course and not necessarily the speed at which it is completed. I am looking more for a platform to perform my electronic and software experiments. Going slower will make some of those experiments easier. I might switch out the drive motors in the future to make it a little bit faster. Even though it might not complete the course at the highest speed, the rover should still look pretty cool as it runs the course. Getting other people interested in robotics, especially young people, is another goal of running the rover in the competition. I also like the construction method you used to build Sawppy and the experience of building my own should help me with future robot designs of my own.

Closed 2019-07-21.

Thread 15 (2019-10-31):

.prt files

Divepit, 2019-10-31:
Hey Sawppy team!

We're looking to build our own version of Sawppy but would like to replace the Aluminum profiles with cylindrical carbon fiber tubes. Would you be willing to share the .prt files with us so we could directly adjust them? Of course we'd be more than happy to share the outcome with you guys as well!

Cheers,
Marco and David

adamgreen, 2019-10-31:
Does the OnShape link at the bottom of [this page](https://github.com/Roger-random/Sawppy_Rover#other-project-resources) not give you CAD file access you need? I believe that there is still a free level for OnShape.

Roger-random, 2019-11-25:
Any update, @Divepit ? As @adamgreen stated, the original Sawppy CAD file is a Onshape document set to be publicly viewable by anyone.

https://cad.onshape.com/documents/43678ef564a43281c83e1aef/w/392bbf8745395bc24367a35c/e/4a687fb6a85c60c7ec293eb2

You are welcome to make a copy and customize for cylindrical carbon fiber tubes.

writemecas, 2020-02-13:
Hi there,

wanted to give an update for everyone trying to download the model. You can, you just need an Onshape account. There is an option to create a free (hobby/maker) account so no subscription needed. Then just select the tap you want, right click an download.

Cheers!

Roger-random, 2020-03-08:
I've confirmed the Onshape free plan is still available, just not prominently promoted which is not surprising for a product that doesn't generate revenue for the company.
https://www.onshape.com/products/free

https://newscrewdriver.com/2018/12/30/onshape-is-free-for-makers-but-theyre-less-eager-to-say-so-now/

Closed 2020-03-08.

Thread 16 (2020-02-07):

LX-16A Servo not available online from Amazon.

TheMightyCodeCoder, 2020-02-07:
Hello Sawppy_Rover team.  I ordered one LewanSoul LX-16A Servo on Amazon and received it.  However, I went back to order more and Amazon is out and says that it doesn't know when they will become available.  I am also having trouble finding the LewanSoul Bus Linker.  I am speculating that this is a Coronavirus thing that's affecting the distribution of these.  If I order straight from China the shipping is very expensive.  Anyone have any idea where I can get these pieces locally?

adamgreen, 2020-02-08:
I placed 2 orders for LX-16A servos this past summer. Between the two orders, they were temporarily out of stock for a bit so I had to wait. I will keep my fingers crossed for you that you have the same luck.

Roger-random, 2020-02-10:
It's quite possible the latest scare has disrupted flow of logistics, but I can tell you this has happened before even without a medical scare. Since the time I started this project I have noticed LX-16A and/or debug board occasionally running out of stock on Amazon with no estimated restock date. These periods of scarcity lasts a few weeks, roughly the time we'd expect a shipping container to travel across the Pacific.

If you have the luxury of a few weeks of time, you should be able to wait out the dry spell. If not, it's time to get creative to adapt other actuators to drive your Sawppy.

I am not aware of other LX-16A retailers within continental United States.

adamgreen, 2020-02-10:
When I just checked, there were 2 of the LX-16A with the not required brackets in stock:
https://www.amazon.com/LewanSoul-Real-Time-Feedback-Bearing-Brackets/dp/B0748BQ49M

adamgreen, 2020-03-04:
@TheMightyCodeCoder  I just checked and it looks like you can pre-order now for a March 12th in-stock date:
https://www.amazon.com/LewanSoul-Real-Time-Feedback-Position-Temperature/dp/B073WR3SK9

Roger-random, 2020-03-04:
And the asking price has gone up from $14.99/ea to $16.99/ea. Roughly what we expected to see for increased tariffs imposed by the current U.S. administration.

adamgreen, 2020-03-08:
Amazon says that they are now in stock.

Roger-random, 2020-03-08:
Amazon shows that for me as well! We have waited through this drought. Closing this issue until the next time...

Closed 2020-03-08.

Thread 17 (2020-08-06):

Parts list missing qty of 608 bearings

nbering, 2020-08-06:
I'm willing to do a PR for the addition, but while I was putting together my parts orders, I had trouble getting a count for the bearings.

If I'm not mistaken, the bearings qty breaks down as:

| Assembly | Assembly Qty. | Bearing Qty. | Subtotal |
| --- | --- | --- | --- |
| Steering Knuckle | 4 | 2 | 8 |
| Fixed Knuckle | 2 | 1 | 2 |
| Corner Steering Joints | 2 | 2 | 4 |
| Suspension Bogie Joints | 2 | 2 | 4 |
| Suspension Rocker Joints | 2 | 2 | 4 |
| **Grand Total** | | | 22 |

I'm not sure if my count is entirely accurate, because some of the part installation instructions are inconsistent as to whether the bearing count is for all instances of that assembly, or per-assembly. Steering knuckle in particular looks like it shows 2-per assembly but says "2 bearings". Fixed knuckle lists 2 bearings as well, but it's hard to tell from the photos if that's 2 per-assembly or total.

nbering, 2020-08-06:
Don't know how I missed this. I've been over the docs a few times but never saw this master parts list.

https://github.com/Roger-random/Sawppy_Rover/blob/master/docs/Parts%20List.md#hardware

Roger-random, 2020-08-09:
It's one thing to have information written down, but it's even harder to organize everything well so people who need the information can find them. Obviously I'm not there yet, but I'm glad you found it eventually.

nbering, 2020-08-09:
Just as feedback, the two places I would have found the qty breakdown helpful:
- The [Amazon list](https://github.com/Roger-random/Sawppy_Rover/blob/master/docs/AmazonAssociate.md)
- The [components list](https://github.com/Roger-random/Sawppy_Rover/tree/master/docs#mass-produced-components), where it describes the requirements for the 608 bearings

Closed 2020-08-06.

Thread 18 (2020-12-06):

TTL Board Amazon Associates Link

ninjix, 2020-12-06:
The TTL Board Amazon Associates link no longer points to a controller. It now shows a LewanSoul LX-224 Serial Bus Servo.

adamgreen, 2020-12-07:
I can't find it on Amazon right now either. Sometimes they run out of stock of the LewanSoul parts and they take the listing down and then it pops back up again in a month or two when they get more in.

The servos can be controlled without this board. I have interfaced a mbed-LPC1768 microcontroller directly to the LX-16A servos on my Sawppy rover so I know it can be done. I don't know if an example of directly connecting them to an AVR based Arduino has been documented yet though.

Patronics, 2020-12-07:
Not an ideal solution, but it seems that the x5 pack option of LX-224 servos in that listing does come with one.

Roger-random, 2020-12-07:
Thank you for pointing this out. I can't find a replacement link either, so I'll leave it as-is until I find a replacement and hope it comes back after some time.

The sporadic availability is a recurring problem, so I'm planning to use something else for the next Sawppy version.

ninjix, 2020-12-07:
Thanks, Roger. Is there a `Develop` branch somewhere we can help you?

nbering, 2020-12-07:
I'd have loved to support you more by using the affiliate links where I could, but had similar issues. Availability in Canada is somewhat different from US Amazon.

For LX-16A specifically, I ended up ordering from AliExpress. Amazon listings with good prices seemed to have low, or no availability. And those with good availability had much higher prices than the $500 design goal would allow for.

adamgreen, 2020-12-08:
Looks like it might be available again under a new link:
https://www.amazon.com/Parts-Accessories-Linker-LX-16A-Controller/dp/B08B5T7JX5/

Roger-random, 2020-12-10:
Wow, they are asking $30 for what was formerly a $10 item. At that point it's tempting to pay $90 and get the LX-16A five-pack, which includes one of those boards along with five servos.

Playville, 2020-12-10:
Abou a year ago I ordered a bunch of LX-16a directly at Lewansoul. Having around 8-10 Motors left, so if anybody urgently need some of those, will give them to other “Sawppyians” for the price I paid once, was about 15€ I guess.

Roger-random, 2020-12-10:
Also: thank you @ninjix and @nbering for your willingness to help. Right now the most valuable contribution I can receive are information from Sawppy builders outside of the United States. I want to switch Sawppy V2 away from parts that have proven to be hard to get. I'm brainstorming alternatives and I would love to get your perspective.

I have activated GitHub's new beta "Discussions" feature, let's all take it for a test drive! Here's the link: #20

ninjix, 2021-01-04:
Looks like a couple TTL boards came back into stock.
https://www.amazon.com/gp/product/B073WRLJB2

Roger-random, 2021-01-10:
Confirmed - the $10 listing (not the scandalous $30 listing) is back in stock and online. All links from Sawppy documentation appear to be working again, both affiliated and non-affiliate links.

Thanks, everyone!

Closed 2021-01-10.

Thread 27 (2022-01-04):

Interest in supporting BLDC motors?

samuk, 2022-01-04:
Hi would you be interested in working on BLDC motor support? I'd personally be interested in the Ros2 version, but Arduino control may be possible too?

More on the idea here: https://github.com/mgonzs13/ros2_rover/issues/2

Roger-random, 2022-01-07:
I have no objection to BLDC motor support, but it won't be the highest priority for development. In order to verify and test the functionality, I'll have to buy BLDC motors and controllers myself. I can't justify that expense at the moment.

I followed your link and I see pointers to motors designed for camera gimbal mounts. Usually, such motors are not suited for driving vehicle wheels due to low torque. Do you plan to use a gearbox?

I am suspicious of the motor specifications listed. It says "230g" of torque, but grams are the wrong unit to express torque.

nbering, 2022-01-07:
I'm interested in at least giving it a try. I'm planning to order a few BLDC motors and something to control to do some controlled experimentation for my own experience.

My focus with BLDC research so far has been for field-oriented-control on actuators for an arm. Simply replacing the serial drive servos isn't something I'd investigated yet, but since a simple ESC reduces the complexity over FOC application boards, it might be more economical for wheel drive than what I'd been seeing for actuators.

Most controllers I'd seen were 1 or 2 channels, though. So that'd be my next concern after torque - that the electronics might get a little complex and/or specialized.

samuk, 2022-01-07:
@Roger-random Thanks, I'll poke at the idea a bit and see if we can get something working. I opened a discussion here https://github.com/samuk/Sawppy_Rover/discussions/3 if anyone wants to chat further on it.

@nbering one of the ideas with https://rosmo.io/ is that the driver boards are 'stackable' on the [M5stack profile](https://shop.m5stack.com/collections/stack-series) so we _hope_ we could stack 3x of the ESC boards on a single ESP32 for 6x6 control. This is all theoretical at this point. But we hope it's going to work! Ordering the first batch of boards some time next week.

Closed 2022-01-07.

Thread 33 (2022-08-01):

Schematic is missing ground plane for +5V voltage regulator

Roger-random, 2022-08-01:
Schematic diagram is missing the ground plane for +5V voltage regulator. There's no connection to battery negative, and no connection to Raspberry Pi ground plane.

Spotted by [Jeffery Reedy], thanks Jeff!

A text warning errata has been added to the documentation just below the schematic. This issues tracks the need to replace the flawed schematic diagram with a corrected one.

Closed 2022-08-24.

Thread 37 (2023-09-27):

Issues with Clip 2n125 Clip 3n20

lolia-olu, 2023-09-27:
Hi,

We're using a Cura Lulz bot to 3D print the parts, however, for clips 2n125 and 3n20, we're experiencing some difficulty during printing as they are not printing smoothly. What extruder would you prefer we print with and is there anything else you think we should be aware of when printing the clips?

Thank you.

adamgreen, 2023-09-29:
I printed mine out of PETG on a Prusa MK3S, the same used for the rest of the parts. I did hit a few issues:
* I needed to print a large number of them at once so that each layer would take long enough to let the previous layer cool before starting the next one. Looks like I printed 20 of the 3n20 and 50 of the 2n125 ones according to the .3mf files I still have kicking around from those builds.
* I used a textured PEI surface for most of the other parts but the clips just didn't have enough bottom layer surface area to stick reliably to this surface so I switched and used my smooth PEI surface for the clips instead.

I still got some blobbing and a bit of warping but I still ended up with enough good ones to put together my printer. They don't need to be perfect to do the job needed and they can't really be seen anyway. Actually some of the oddness in the shape made them fit a bit more snug in the channel anyway :)

lolia-olu, 2023-10-05:
Thank you @adamgreen and @Roger-random. Very insightful and I will keep these tips in mind.

Closed 2023-10-05.

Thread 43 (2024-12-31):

Print Wheel

Fibo27, 2024-12-31:
Hi, I am using a Creality slicer which is based on Cura. However, it is taking an inordinate amount of time to print the wheels (nearly 18 hours vs 7.5 as you mention). Can you please share the key slicer settings if you can?

Thanks

nbering, 2024-12-31:
The slicer settings and an overview of printing considerations is documented here:
https://github.com/Roger-random/Sawppy_Rover/blob/c9bb17d4c28b7518bbd493eec5f878033b617ee7/docs/Print%20Overview.md

One factor required to establish the print time for these settings was the print and travel speeds. But you could probably infer those from the specs for the printer that was used for the original project parts.

Roger-random, 2024-12-31:
Thank you, Nicholas! Here's a link that should go directly to the slicer setting section on that page you linked:
https://github.com/Roger-random/Sawppy_Rover/blob/main/docs/Print%20Overview.md#stl-slicer-settings

Good point I did not explicitly specify print and travel speeds. I had left those values in my slicer at their default values. Since I didn't look at them, I didn't think to write them down.

Also, a reminder this project is now five years old and I have not made significant updates. (It's been on my to-do list...) Slicer software and 3D printers have changed a lot in that time.

Thank you for your interest and I hope you find success.

Fibo27, 2024-12-31:
Thank you both. The Mars rover has been of an interest to me for a while. Great work done by you.
So far I had been working on getting sensors and software running on a four wheeled robot. With advances in AI and ROS2 in particular, I plan to use Vision Language Model, Text to Speech besides the ROS2 framework. I will be using an Nvidia Jetson Orin given that Rpi and Arduino do not have the same capability. I have all of these working on a four wheeled robot but would like to incorporate it on the rover. CAD and mechanical design is an area that I need to work on more - again thanks for all the work. Wish you a great 2025

Closed 2024-12-31.

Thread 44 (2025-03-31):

Sawppy Build with Ros2

Fibo27, 2025-03-31:
@Roger-random - many thanks for an awesome project that you started some years back - its still relevant now. Following my previous issue, i have managed to build sawppy and kitted it out with a number of sensors. It has a 1) Lidar, 2) IMU, 3) RGB Camera, Motors with Encoders. I had to modify the wheel and the knuckle joints for the steering wheels as the heat inserts were creating issues and i have used shaft couplers. Since this was my first mechanical project (i used to use small robot kits earlier), I had to go through the learning curve of cutting shafts and adding indents, making grooves for retainer clips using a dremel and a power drill as you have instructed - i can see the errors in the set-up which i will rectify as i use the rover more. That being said, the key thing is the compute platform which is a Jetson Orin device and it runs Ros2. The data gets transmitted and I have a server that has a larger compute and uses the data sent across by the rover to visualize the rover in Rviz and navigate using Nav2 module of Ros2. In addition, there were many more learning on the software side namely: dockers, remote access, video to text, text to speech during navigation, ackerman steering...
Again - many thanks!

Roger-random, 2025-03-31:
Thank you for your message! When I shared Sawppy I had no idea if anyone would accept my invitation to build their own. It is tremendously rewarding to read messages like yours. I'm glad you enjoyed building your own rover and found it educational.

Are you sharing your rover adventures publicly online anywhere I can see? (Blog, social media, etc.) I always love to see stories of other Sawppy rovers in the world.

Fibo27, 2025-03-31:
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

Here you go. I understand that some folks have updated the hackaday blig post with their version. I plan to do that at some point in time. I also came across the slack channel where those who are building the osr collaborate but haven't posted any comment.

Fibo27, 2025-03-31:
Adding to my lack of mechanical skills: I had to spoof the starting point of the servos by physically aligning the wheels at the time of start-up and using that position as the center position for each steering wheel. This was necessitated as the steering shafts are not as perfect and are also not connected to the servo when it reads 500 (the center position) - so i have done that using software and it works like a charm!

Roger-random, 2025-04-01:
Thank you for sharing the picture! I love seeing Sawppy rovers built by others. Each one is a reflection of their builder's journey.

Closed 2025-04-01.

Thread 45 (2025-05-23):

Question/issue with cad file - Bogie Wheels

knickels, 2025-05-23:
Not sure if this is the right place to post this - if not, steer me to it please :)

Starting to build a copy of Sawppy for my lab.  I noticed in [the onshape file](https://cad.onshape.com/documents/43678ef564a43281c83e1aef/w/392bbf8745395bc24367a35c/e/9bd6bbb7aba50a97523d14f2)
 that the side holes in the Bogie Wheels part don't go all the way through.

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

There are two steps in the time line, "Bogie Mid Side Washers Bridge Assist" and "Bogie Rear Side Washers Bridge Assist" that appear to actually add an 0.5mm bridge between the washers and the bolt hole.  I guess I could print as-is and then drill it out, but I'm wondering what the purpose of these bridges are.
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

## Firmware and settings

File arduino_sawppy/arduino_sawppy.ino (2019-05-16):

/*
 * Arduino sketch to drive a Sawppy rover using a joystick (two potentiometers)
 * wired to analog pins. After calculations based on rover geometry, resulting
 * angle and velocity information can be sent to different types of outputs.
 *
 * http://sawppy.com
 *
 * LewanSoul serial bus servo control code (in lewansoul.cpp) subject to LewanSoul terms and conditions.
 *
 * Remaining code created by Roger Cheng are released under MIT license.
 */

#include <math.h>
#include "Arduino.h"
#include "joydrive.h"
#include "lewansoul.h"

// Output select - only one of the following should be uncommented
#define LEWANSOUL 1 // Output to LewanSoul serial bus servo commands
//#define PRINTCMD 1 // Output to serial debug monitor
// Output select end

#define STEERING_PIN 1 // Analog pin to control steering angle
#define VELOCITY_PIN 0 // Analog pin to control speed
#define INPLACE_BUTTON 2 // Button to trigger turn-in-place mode.

// Initialize joystick module
JoyDrive jd(STEERING_PIN, VELOCITY_PIN);

#ifdef LEWANSOUL
LewanSoul lss(false);
#endif

// Hold information about wheel arrangement on rover. This information
// is fixed and does not change while the program runs.
typedef struct RoverWheel
{
  float x; // How far this wheel is to the right (positive) or left (negative) of center
  float y; // How far this wheel is to the ahead (positive) or behind (negative) center
  int rollServoId; // Serial bus ID of servo responsible for wheel rolling
  bool rollServoInverted; // Whether to invert wheel rolling front/back direction
  int steerServoId; // Serial bus ID of servo responsible for wheel steering
  float steerTrim; // Adjustment in angle degrees to trim steering center position
} RoverWheel;

// Array of wheels on rover
const RoverWheel Chassis[] = {
  // front left
  {
    -9.125, // x
    11.375, // y
    25,     // roll ID
    false,  // roll inverted
    23,     // steer ID
    -4      // steer trim
  },
  // front right
  {
     9.125, // x
    11.375, // y
    27,     // roll ID
    true,   // roll inverted
    29,     // steer ID
    -4      // steer trim
  },
  // mid left
  {
    -10.375,// x
    0,      // y
    21,     // roll ID
    false,  // roll inverted
    -1,     // steer ID
    0       // steer trim
  },
  // mid right
  {
    10.375, // x
    0,      // y
    22,     // roll ID
    true,   // roll inverted
    -1,     // steer ID
    0       // steer trim
  },
  // rear left
  {
    -9,     // x
    -10,    // y
    20,     // roll ID
    false,  // roll inverted
    24,     // steer ID
    2       // steer trim
  },
  // rear right
  {
     9,     // x
    -10,    // y
    28,     // roll ID
    true,   // roll inverted
    26,     // steer ID
    4       // steer trim
  }
};

// Index into Chassis[] used for calculating steering angles
#define FRONT_LEFT 0
#define FRONT_RIGHT 1
#define MID_LEFT 2

// Using information above, the maximum steering angle for a front wheel
float maxSteering;

// Store calculation of servo angle and speed before we send them as commands
// Also stores turning radius (hypotenuse in trig calculations) which affects speed.
// This information is updated on every loop.
typedef struct ServoCommand {
  float angle;
  float radius;
  float speed;
} ServoCommand;

ServoCommand servoCommands[6];

// Enumeration tracking current state of rover control
enum RoverState { driving, enterTurnInPlace, turnInPlace, enterDriving };

enum RoverState state = driving;
unsigned long stateChangeStart; // track time in transition for enterX states
#define WAIT_FOR_STOP 600 // number of milliseconds from stateChangeStart to ensure we're stopped.
#define WAIT_TRANSITION 1000 // number of milliseconds from stateChangeStart for a transition. Should be greater than WAIT_FOR_STOP

// Use the servoCommands[].radius values to scale all servoCommands[].speed relative
// to a given velocity.
void speedFromRadius(float maxSpeed)
{
  int wheel; // iterator for wheels on a chassis
  float maxRadius = 0.0; // Turning radius of wheel furthest from turn center

  // Find maximum radius of all wheels
  for (wheel = 0; wheel < 6; wheel++)
  {
    if (abs(servoCommands[wheel].radius) > maxRadius)
    {
      maxRadius = abs(servoCommands[wheel].radius);
    }
  }

  if (maxRadius > 0)
  {
    // Max radius found, now scale all wheel speeds so those with max radius spins
    // at commanded velocity and other wheels at slower speed based on radius ratio.
    for (wheel = 0; wheel < 6; wheel++)
    {
      servoCommands[wheel].speed = (servoCommands[wheel].radius/maxRadius)*maxSpeed;
    }
  }
  else
  {
    // No radius information to work with, every wheel gets same speed.
    for (wheel = 0; wheel < 6; wheel++)
    {
      servoCommands[wheel].speed = maxSpeed;
    }
  }
}

// Turn in place mode: point all wheels at center so we can rotate about center.
void wheelsToTurnInPlace()
{
  for (int wheel = 0; wheel < 6; wheel++)
  {
    // Calculate angles to point at center
    if (Chassis[wheel].y == 0)
    {
      servoCommands[wheel].angle = 0;
      servoCommands[wheel].radius = abs(Chassis[wheel].x);
    }
    else
    {
      servoCommands[wheel].angle = -atan(Chassis[wheel].y/Chassis[wheel].x)*180.0/M_PI;
      servoCommands[wheel].radius = sqrt(pow(Chassis[wheel].x,2)+pow(Chassis[wheel].y,2));
    }

    // When turning in place, one side wheels turn opposite the other. Change direction of
    // this inequality comparison to reverse turn-in-place direction relative to joystick.
    if (Chassis[wheel].x > 0)
    {
      servoCommands[wheel].radius *= -1;
    }
  }
}

// All wheels to default position: pointing straight ahead and at given velocity
void wheelsToDefault(int velocity)
{
  for (int wheel = 0; wheel < 6; wheel++)
  {
    servoCommands[wheel].angle = 0;
    servoCommands[wheel].radius = 0;
    servoCommands[wheel].speed = velocity;
  }
}

// Runs once upon powerup
void setup()
{
  // Configure button pins
  pinMode(INPLACE_BUTTON, INPUT);
  digitalWrite(INPLACE_BUTTON, HIGH); // Button pulls LOW when pressed

#ifdef LEWANSOUL
  // LewanSoul serial servo code is taking over Serial port.
  lss.setup();
#endif

#ifdef PRINTCMD
  // Use serial port to print our calculated commands
  Serial.begin(9600);
#endif

  // Calculate maximum steering angle
  float adjacent = Chassis[MID_LEFT].x - Chassis[FRONT_LEFT].x;
  float opposite = Chassis[FRONT_LEFT].y;
  maxSteering = abs(atan(opposite/adjacent)*180.0/M_PI);

  // Start in driving state
  state = driving;
}

// Runs regularly as long as there is power to Arduino
void loop()
{
  int steering; // -100 to 100, retrieved by JoyDrive::getSteering()
  int velocity; // -100 to 100, retrieved by JoyDrive::getVelocity()
  int wheel; // Iterator index
  float turnCenterX; // Position of center of turn, which lies on the X axis
  float inRadians; // Angle calculation in radians

  int invert; // Multiplier for implementing RoverWheel.rollServoInverted
  int referenceWheel; // Wheel used to calculate turnCenterX

  bool triggerStateChange = (digitalRead(INPLACE_BUTTON) == LOW); // Read button that commands turn-in-place mode.
  delay(100);
  steering = jd.getSteering(); // Read steering potentiometer
  delay(100);
  velocity = jd.getVelocity(); // Read velocity potentiometer

#if PRINTCMD
  Serial.print("S");
  Serial.print(steering);
  Serial.print(" V");
  Serial.print(velocity);
  Serial.print(" ");
#endif

  // State changes can only be triggered when going slowly or stopped
  if (triggerStateChange && abs(velocity) < 10 && abs(steering) < 10)
  {
    if (state == driving)
    {
      // If we were slowed, command a stop now, and start our transition timer.
      velocity = 0;

      stateChangeStart = millis();
      state = enterTurnInPlace;
    }
    else if (state == turnInPlace)
    {
      // If we were slowed, command a stop now, and start our transition timer.
      velocity = 0;

      stateChangeStart = millis();
      state = enterDriving;
    }
  }

  if (state == enterTurnInPlace)
  {
    velocity = 0;
    if (millis() > stateChangeStart + WAIT_TRANSITION && !triggerStateChange)
    {
      // We've waited long enough for everything to settle
      // and button has been released.
      state = turnInPlace;
    }
    else if(millis() > stateChangeStart + WAIT_FOR_STOP)
    {
      // We should be at full stop now, turn corner wheels.
      wheelsToTurnInPlace();
    }
    speedFromRadius(0);
  }

  if (state == enterDriving)
  {
    velocity = 0;
    if (millis() > stateChangeStart + WAIT_TRANSITION && !triggerStateChange)
    {
      // We've waited long enough for everything to settle
      // and button has been released.
      state = driving;
    }
    else if(millis() > stateChangeStart + WAIT_FOR_STOP)
    {
      // We should be at full stop now, turn corner wheels.
      wheelsToDefault(0);
    }
    speedFromRadius(0);
  }

  if (state == turnInPlace)
  {
    wheelsToTurnInPlace();

    // Calculate speed from relative radii
    speedFromRadius(steering);
  }

  if (state == driving)
  {
    // Choose a reference wheel and, from there, calculate turn center X
    if (steering == 0)
    {
      // Rolling straight ahead or behind
      referenceWheel = -1;
      turnCenterX = 0;
    }
    else
    {
      if (steering > 0)
      {
        referenceWheel = FRONT_RIGHT;
      }
      else
      {
        referenceWheel = FRONT_LEFT;
      }

      // Rover motion is based on joystick commanding angle of reference wheel
      servoCommands[referenceWheel].angle = maxSteering * steering / 100.0;

      // From there, calculate the center of rotation we'll use to calculate remaining wheels
      inRadians = servoCommands[referenceWheel].angle * M_PI / 180.0;
      turnCenterX = Chassis[referenceWheel].x + (Chassis[referenceWheel].y / tan(inRadians));

      // Store length of hypotenuse for later speed calculation
      servoCommands[referenceWheel].radius = abs(Chassis[referenceWheel].y / sin(inRadians));
    }

    // Calculate other wheel angles based on turn center X
    for (wheel = 0; wheel < 6; wheel++)
    {
      if (turnCenterX == 0)
      {
        // Rolling straight ahead or behind
        servoCommands[wheel].angle = 0;
        servoCommands[wheel].speed = velocity;
      }
      else if (wheel != referenceWheel)
      {
        // The X-axis distance between this wheel and turn center
        float wheelToCenter = turnCenterX - Chassis[wheel].x;

        if (Chassis[wheel].steerServoId != -1)
        {
          // Calculate wheel angle
          inRadians = atan(Chassis[wheel].y/wheelToCenter);

          // Convert to degrees and store command
          servoCommands[wheel].angle = inRadians*180.0/M_PI;

          // Store hypotenuse (turning radius) in speed for later calculation.
          servoCommands[wheel].radius = abs(Chassis[wheel].y/sin(inRadians));
        }
        else
        {
          // No steering servo, but good to blank out data anyway.
          servoCommands[wheel].angle = 0;

          // This wheel lacks steering servo. This should only happen on the wheels
          // aligned with turn axis. (wheel coordinate y of zero.) So their turning
          // radius ("hypotenuse" in all the other trig calculations) becomes their
          // X relative to turn center.
          servoCommands[wheel].radius = abs(wheelToCenter);
        }
      }
    }

    if (abs(turnCenterX) > 0)
    {
      // Calculate speed from relative radii
      speedFromRadius(velocity);
    }
  }
  
#ifdef LEWANSOUL
  // All angles and speeds calculated, send the commands accounting
  // for steering trim offset and inverting speed where needed
  for (wheel = 0; wheel < 6; wheel++)
  {
    if (Chassis[wheel].steerServoId != -1)
    {
      lss.moveTo(Chassis[wheel].steerServoId, servoCommands[wheel].angle + Chassis[wheel].steerTrim);
    }

    if (Chassis[wheel].rollServoInverted)
    {
      invert = -1;
    }
    else
    {
      invert = 1;
    }
    lss.spinAt(Chassis[wheel].rollServoId, servoCommands[wheel].speed * invert);
  }
#endif

#ifdef PRINTCMD
  for (wheel = 0; wheel < 6; wheel++)
  {
    Serial.print(" W");
    Serial.print(wheel);
    Serial.print(" ");
    if (Chassis[wheel].steerServoId != -1)
    {
      Serial.print(servoCommands[wheel].angle + Chassis[wheel].steerTrim);
      Serial.print("deg ");
    }

    if (Chassis[wheel].rollServoInverted)
    {
      invert = -1;
    }
    else
    {
      invert = 1;
    }
    Serial.print(servoCommands[wheel].speed * invert);
    Serial.print("pct ");
  }
  Serial.println();
#endif

}

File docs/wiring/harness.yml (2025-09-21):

connectors:
  X1a: &jst3p # define template for JST 3-pin connector
    type: JST
    subtype: female
    pinlabels: [Sig, 5V, GND]
    show_pincount: true
    image:
      src: ./connector_images/jst-2.0-3p.jpg
      caption: JST-2.0-3P Pinout
      width: 200
      height: 200
  X1b:
    <<: *jst3p # create from template
  X2a:
    <<: *jst3p # create from template
  X2b:
    <<: *jst3p # create from template
  X3a:
    <<: *jst3p # create from template
  X3b:
    <<: *jst3p # create from template
  X4a:
    <<: *jst3p # create from template
  X4b:
    <<: *jst3p # create from template
  X5a:
    <<: *jst3p # create from template
  X5b:
    <<: *jst3p # create from template

cables:
  W82: 
    gauge: 26 awg
    length: 82 cm
    colors: [RD, BK, YE]
  W50: 
    gauge: 26 awg
    length: 50 cm
    colors: [RD, BK, YE]
  W64: 
    gauge: 26 awg
    length: 64 cm
    colors: [RD, BK, YE]
  W36: 
    gauge: 26 awg
    length: 64 cm
    colors: [RD, BK, YE]
  W21: 
    gauge: 26 awg
    length: 64 cm
    colors: [RD, BK, YE]


connections:
  -
    - X1a: [1-3]
    - W82: [1-3]
    - X1b: [1-3]
  -
    - X2a: [1-3]
    - W50: [1-3]
    - X2b: [1-3]
  -
    - X3a: [1-3]
    - W64: [1-3]
    - X3b: [1-3]
  -
    - X4a: [1-3]
    - W36: [1-3]
    - X4b: [1-3]
  -
    - X5a: [1-3]
    - W21: [1-3]
    - X5b: [1-3]

metadata:
  title: Servo Harness 

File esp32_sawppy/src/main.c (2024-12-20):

/*

Main startup for Sawppy Rover ESP32 controller

Copyright (c) Roger Cheng

MIT License

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
*/
#include "freertos/FreeRTOS.h"
#include "freertos/queue.h"
#include "freertos/task.h"

#include <joy_msg.h>
#include <twist_msg.h>
#include <wheel_msg.h>
#include <msg_print.h>

#include "gpio_assignments.h"

#ifdef USE_JOY_ADC
#include <joy_adc.h>
#endif
#ifdef USE_JOY_RMT_RC
#include <joy_rmt_rc.h>
#endif

#include "volt_adc.h"

#ifdef USE_WIFI
#include "softap_start.h"
#include "station_start.h"
#include "http_file_server.h"
#endif

#include <joy_steer.h>
#include <wheel_ackermann.h>
#include <servo_steer_ledc.h>
#include <drv8833_mcpwm.h>

void app_main()
{
  QueueHandle_t xJoystickQueue = xQueueCreate(1, sizeof(joy_msg));
  QueueHandle_t xCmdVelQueue = xQueueCreate(1, sizeof(twist_msg));
  QueueHandle_t xWheelQueue = xQueueCreate(1, sizeof(wheel_msg));
  QueueHandle_t xPowerQueue = xQueueCreate(1, sizeof(power_msg));

#ifdef USE_WIFI
  ESP_ERROR_CHECK(esp_event_loop_create_default());
  http_file_server_task_parameters http_params = {
    .xJoystickQueue = xJoystickQueue,
    .xPowerQueue = xPowerQueue,
  };
#endif

  joy_steer_task_parameters joy_steer_params = {
    .xJoyMsgQueue = xJoystickQueue,
    .xCmdVelQueue = xCmdVelQueue,
  };

  wheel_ackermann_task_parameters wheel_ackermann_params = {
    .xCmdVelQueue = xCmdVelQueue,
    .xWheelQueue = xWheelQueue,
  };

  if (NULL == xJoystickQueue || NULL == xCmdVelQueue || NULL == xWheelQueue || NULL == xPowerQueue)
  {
    printf("ERROR: Queue allocation failed.");
  }
  else
  {
#ifdef USE_JOY_ADC
    xTaskCreate(joy_adc_read_task, "joy_adc_read_task", 2048, xJoystickQueue, 20, NULL);
#endif

#ifdef USE_JOY_RMT_RC
    xTaskCreate(joy_rmt_rc_read_task, "joy_rmt_rc_read_task", 2048, xJoystickQueue, 20, NULL);
#endif

#ifdef USE_WIFI
    xTaskCreate(softap_start_task, "softap_start_task", 1024*3, NULL, 20, NULL);
    //xTaskCreate(station_start_task, "station_start_task", 1024*3, NULL, 20, NULL);
    xTaskCreate(http_file_server_task, "http_file_server_task", 1024*4, &http_params, 19, NULL);

    xTaskCreate(volt_adc_task, "volt_adc_task", 2048, xPowerQueue, 10, NULL);
    //xTaskCreate(power_msg_print_task, "power_msg_print_task", 2048, xPowerQueue, 14, NULL);
#endif

    //xTaskCreate(joy_msg_print_task, "joy_msg_print_task", 2048, xJoystickQueue, 25, NULL);
    xTaskCreate(joy_steer_task, "joy_steer_task", 2048, &joy_steer_params, 15, NULL);
    //xTaskCreate(twist_msg_print_task, "twist_msg_print_task", 2048, xCmdVelQueue, 25, NULL);
    xTaskCreate(wheel_ackermann_task, "wheel_ackermann_task", 2048, &wheel_ackermann_params, 14, NULL);
    //xTaskCreate(wheel_msg_print_task, "wheel_msg_print_task", 2048, xWheelQueue, 25, NULL);
    xTaskCreate(servo_steer_ledc_task, "servo_steer_ledc_task", 2048, xWheelQueue, 13, NULL);
    xTaskCreate(drv8833_mcpwm_task, "drv8833_mcpwm_task", 2048, xWheelQueue, 12, NULL);
  }
}

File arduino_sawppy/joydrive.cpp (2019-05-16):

/* 
  *  JoyDrive = Joystick Drive
  * ------------
  *
  * Reads two analog pins that are connected to potentiometers representing two
  * axis of a joystick. One axis represents steering angle, one axis represents
  * velocity. Each is normalized within a range from -100 to 100, so the sign
  * represents direction and number represents magnitude as a percentage.
  * 
  */

#include "joydrive.h"

JoyDrive::JoyDrive(int steeringPin, int velocityPin)
{
  _steeringPin = steeringPin;
  _velocityPin = velocityPin;
  _previousSteering = 0;
  _previousVelocity = 0;
}

int JoyDrive::getSteering()
{
  // analogRead returns between 0 and 1023
  int steeringRaw = analogRead(_steeringPin);
  int steeringNormalized  = normalized(steeringRaw, STEER_MID, INVERT_STEERING);
  int steeringConstrained = constrained(steeringNormalized, _previousSteering, MAX_DELTA_STEERING);

  _previousSteering = steeringConstrained;

  return steeringConstrained;
}

int JoyDrive::getVelocity()
{
  // analogRead returns between 0 and 1023
  int velocityRaw = analogRead(_velocityPin);
  int velocityNormalized = normalized(velocityRaw, VEL_MID, INVERT_VELOCITY);
  int velocityConstrained = constrained(velocityNormalized, _previousVelocity, MAX_DELTA_VELOCITY);

  _previousVelocity = velocityConstrained;

  return velocityConstrained;
}

// The normalized() function accepts a value in the full range of ADC (0-1023) and
// turns it into a range from -100 to 100 with 0 at the given midpoint.
int JoyDrive::normalized(int raw, int midpoint, bool invert)
{
  float range = ADC_MID - DEAD_ZONE;
  float sign = 0.0;
  int subset = 0;
  int normalized = 0;
  
  if (raw > midpoint + DEAD_ZONE)
  {
    sign = 100.0;
    subset = raw - midpoint - DEAD_ZONE;
  }
  else if (raw < midpoint - DEAD_ZONE)
  {
    sign = -100.0;
    subset = midpoint - DEAD_ZONE - raw;
  }
  else
  {
    sign = 100.0;
    subset = 0;
  }

  if (invert)
  {
    sign = sign * -1;
  }

  normalized = sign * subset / range;

  // Due to how midpoint might vary, cap the maximums.
  if (normalized > 100)
  {
    normalized = 100;
  }

  if (normalized < -100)
  {
    normalized = -100;
  }

  return normalized;
}

// The constrained() function accepts a normalized value and returns a
// value that is not more than maxDelta away from previous value.
int JoyDrive::constrained(int normalized, int previous, int maxDelta)
{
  int constrained = 0;

  if (normalized > previous + maxDelta)
  {
    constrained = previous + maxDelta;
  }
  else if (normalized < previous - maxDelta)
  {
    constrained = previous - maxDelta;
  }
  else
  {
    constrained = normalized;
  }

  return constrained;
}

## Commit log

2018-04-16 Initial wheel assembly with steerable and fixed arms.
    [Fixed Arm.stl, LX-16A - Bracket.stl, LX-16A - Coupler.stl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]
2018-04-16 First complete draft of rocker bogie suspension
    [Bogie-Body.stl, Bogie-Wheels.stl, Fixed Arm.stl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]
2018-04-16 Rover Slim Edition
    [Bogie-Body.stl, Bogie-Wheels.stl, Fixed Arm.stl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]
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2018-05-02 Fix spacing issues so M3x8mm bolts can be used throughout.
    [Bogie-Wheels.stl, Fixed Arm.stl, Front Corner.stl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]
2018-05-02 Parts for main body box.
    [Body Corner.stl, BodyMount.stl]
2018-05-02 Battery tray and panel for on/off switch and voltage meter
    [Battery Tray.stl, Power Panel.stl]
2018-05-02 Differential bar
    [DiffBrace.stl, DiffEnd.stl, DiffLink.stl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]
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2018-06-14 Rename suspension knuckles
    [Fixed Knuckle.stl, Steering Knuckle.stl]
2018-06-14 Slimmer fixed knuckle also faces convenient direction for wiring.
    [Fixed Knuckle.stl]
2018-06-14 PETG is more flexible than PLA so make the wheel a little thicker to compensate
    [Wheel.stl]
2018-06-14 PETG required adjusting hole dimension to better fit heat-set inserts.
    [Wheel Hub.stl]
2018-06-14 PETG adjustments
    [LX-16A - Bracket.stl, LX-16A - Coupler.stl]
2018-06-14 With slimmer fixed knuckle, rocker pivot no longer needs to have a cutout for clearance.
    [Rocker.stl]
2018-06-14 M3 nut installation tool
    [Clip2n125.stl, Clip3n20.stl]
2018-06-14 Remove duplicate of Rocker Body Mount.stl
    [BodyMount.stl]
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2018-06-14 Images for 3D printed fixed knuckle
2018-06-14 3D Printed Fixed Knuckle Instructions
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2019-04-21 My 3D model changes
    [25D Coupler.scad, 25D Coupler.stl, AX-12-Bracket.fcstd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]
2019-04-27 My changes moved to the new location
    [25D Coupler.scad, 25D Coupler.stl, AX-12-Bracket.fcstd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]
2019-04-27 Contributions by Marco Walther
    * My 3D model changes
    * Minor formating change
    * My changes moved to the new location
    [25D Coupler.scad, 25D Coupler.stl, AX-12-Bracket.fcstd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]
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2019-06-03 New LED Display
    [DisplayBottom.FCStd, DisplayBottom.stl, DisplayTop.FCStd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]
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2019-07-10 Fix small link typo
    AssemblyBody.md had a "Printed corner pieces" link that didn't show up
    properly because a '0' was placed where a ']' should have been.
2019-07-14 Add M3x16mm socket head screws to parts list
    * 10 M3x16mm screws are used for differential assembly.
    * 6x3 M3x16mm screws are used for attaching wheels to hubs.
    My code editor also removed a few trailing white spaces from other
    lines too.
2019-10-30 Fixed couple of typos noticed during build
    My code editor also automatically removed some trailing whitespace from
    other lines in the same files as well.
2019-11-25 Build note updates
    As I was working on my Sawppy build, I updated the build instructions
    whenever I noticed things that I thought should be corrected or better
    described. This commit contains those updates:
    * Note that wheels are attached with M3x16mm bolts.
    * Updated part list:
    * Reduced number of M3 set screws required from 100 to 22.
    McMaster-Carr sells these set screws in boxes of 25 so I ended up
    with 3 boxes that I didn't need based on the original incorrect
    quantity.
    * Added longer screws required for attaching servo horns to the servo
    couplers.
    * Added a note to the "Print Differential" documentation to indicate
    that the 2 Diff End parts should be mirror images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
2019-11-27 STL orientation links: MatterControl and Meshmixer
    Thanks to David Wheeler (Twitter @dave20874) for investigating the Meshmixer option.
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2020-05-14 MakerBeamXL as alternate, can cut from 2x2m
    Incorporate reports from other Sawppy builders.
    * It is possible to cut everything from two 2-meter segments of extrusions.
    * If Misumi is difficult, alternates are available from MakerBeamXL, AliExpress, etc.
2020-05-15 Illustrating Bogie-Wheels left-right reversed
    Thanks to Tim who was willing to share these pictures
2020-05-15 Errata: left-right reverse Bogie-Wheels
    Thanks to Tim for sharing these pictures (https://hackaday.io/timing2211)
2020-05-15 Add link to Bogie-Wheel reversal errata
2020-05-15 Reword description of middle wheel alignment error
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2021-03-08 Something is wrong with angular velocity calculation
    [main.c]
2021-03-09 Angular velocity math fixes
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2021-03-11 Failing with MCPWM GENERATOR ERROR
    [main.c]
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2021-04-07 WiFi Proof of Concept from ESP32Tests/webserver_play
    [partition_singleapp_spiff.csv]
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2021-04-18 Both Node.JS and ESP32 server publish voltage JSON to client, client JS parses and displays it.
2021-05-18 Add note about detent depth
    I had some issues with detents being too shallow, because I got lazy with the file. For the wheel hub in particular, this can cause the set screw to stick out too far and interfere with the wheel's installation.
2021-05-31 Bump ws from 7.4.4 to 7.4.6 in /esp32_sawppy/browser_ui
    Bumps [ws](https://github.com/websockets/ws) from 7.4.4 to 7.4.6.
    - [Release notes](https://github.com/websockets/ws/releases)
    - [Commits](https://github.com/websockets/ws/compare/7.4.4...7.4.6)
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2022-08-01 Schematic errata: regulator missing ground
    Add a text warning errata until a new schematic can be generated, tracked as
    #33
2022-08-24 Schematic edited for 5V regulator ground wire, fixes #33
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2022-11-11 Bump minimatch from 3.0.4 to 3.1.2 in /esp32_sawppy/browser_ui
    Bumps [minimatch](https://github.com/isaacs/minimatch) from 3.0.4 to 3.1.2.
    - [Release notes](https://github.com/isaacs/minimatch/releases)
    - [Commits](https://github.com/isaacs/minimatch/compare/v3.0.4...v3.1.2)
    ---
    updated-dependencies:
    - dependency-name: minimatch
    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
2022-11-11 Bump ansi-regex from 4.1.0 to 4.1.1 in /esp32_sawppy/browser_ui
    Bumps [ansi-regex](https://github.com/chalk/ansi-regex) from 4.1.0 to 4.1.1.
    - [Release notes](https://github.com/chalk/ansi-regex/releases)
    - [Commits](https://github.com/chalk/ansi-regex/compare/v4.1.0...v4.1.1)
    - dependency-name: ansi-regex
    dependency-type: indirect
    ...
    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
2023-07-11 Bump semver from 5.7.1 to 5.7.2 in /esp32_sawppy/browser_ui
    Bumps [semver](https://github.com/npm/node-semver) from 5.7.1 to 5.7.2.
    - [Release notes](https://github.com/npm/node-semver/releases)
    - [Changelog](https://github.com/npm/node-semver/blob/v5.7.2/CHANGELOG.md)
    - [Commits](https://github.com/npm/node-semver/compare/v5.7.1...v5.7.2)
    - dependency-name: semver
    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
2024-06-16 Bump braces from 3.0.2 to 3.0.3 in /esp32_sawppy/browser_ui
    Bumps [braces](https://github.com/micromatch/braces) from 3.0.2 to 3.0.3.
    - [Changelog](https://github.com/micromatch/braces/blob/master/CHANGELOG.md)
    - [Commits](https://github.com/micromatch/braces/compare/3.0.2...3.0.3)
    - dependency-name: braces
    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
2024-06-18 Bump ws from 7.5.9 to 7.5.10 in /esp32_sawppy/browser_ui
    Bumps [ws](https://github.com/websockets/ws) from 7.5.9 to 7.5.10.
    - [Commits](https://github.com/websockets/ws/compare/7.5.9...7.5.10)
    - dependency-name: ws
    dependency-type: direct:production
    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
2025-08-01 adding documention about wiring harness
    [harness.bom.tsv]
2025-08-25 added documentation abouty wiring
    [harness.bom.tsv]
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
